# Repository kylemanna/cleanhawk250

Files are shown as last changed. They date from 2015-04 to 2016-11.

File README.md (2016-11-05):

# CleanHawk 250 Quadcopter Power Distribution Board for Emax 250

This document outlines the basic tasks to get the CleanHawk 250 Power Distribution Board (PDB) up and flying.

**Documentation can be found at the [CleanHawk250 GitHub repository](https://github.com/kylemanna/cleanhawk250).**

## Overview

The goal of the CleanHawk 250 PDB is to simplify wiring and imporve integration and reliability.  The printed circuit board replaces the bottom carbon fiber frame support on the Emax 250 / Nighthawk 250 quadcopters.

### Buy It Now

* [Tindie](http://bit.ly/1HMsioh)
* [Amazon](http://amzn.to/2fEIMti)

### Features

* **3-4S compatible**
* Designed for **KISS 18A ESCs**, ReadyToFly/Witespy's BearHug should fit just fine, and have pads for traditional ESCs. Hoping that the new Emax BLHeli Oneshot ESCs fit.
* **3A @ 5V** for flight computer, OSD, and LEDs (i.e. WS2812), telemetry/BT, etc. (85%+ efficient).
* **3A @ 9V** for FPV camera, vtx, and LEDs. (92%+ efficient),
* **(6) RGB LEDs**. 4 on bottom, 2 on top (not sure if top will be useful). Testing waters here. User configurable color by changing resistors. Plan is to do red on the rear and white up front.
* **FPV LC filter** that can select between 9V or 5V for feeding cameras and FPV transmittter,
* Multiple soldering points for accessories on the VBAT, 9V, and 5V rail. Helps to contain the wiring mess.
* **Battery voltage divider** for dividing the voltage down to something manageable for the Frsky D4R-II.
* Optional bulk capacitance near the ESCs to help smooth out ripples.
* Centralized battery input pads to keep the high current paths through the board as short as possible
* **2oz copper** for efficiency and electroless nickel immersion gold plating for solderability.
* Sufficient copper keep out area surrounding the mounting holes
* Shielded inductors to reduce switching power supply noise.

### What's Included

* (1) CleanHawk 250 Power Distribution Board with all surface mount components installed.
* (1) 1x4 pin header for the auxiliary port
* (1) 1x6 pin header for the ESC and flight controller port
* (3) 2x2 pin header for respective power supply outputs (5V, 9V, Filtered)

### Recommended Additional Components

#### Wire Extension Cables

It is recommended to use Dupont female to female cable connectors to wire the PDB to the receiver and flight controller. Available on [Amazon in 10cm length](http://amzn.com/B00KOL5BCC).

Dupont cables

An alternative to these are male to male servo extension headers such as [these from Amazon](http://amzn.com/B00FGLSTY2).

Servo extension

#### Angled Pin Headers

Consider picking up 90° 0.1" angled pin headers. Single row pin headers aid in mounting KISS ESCs.  Double row pin headers are very useful if the front/rear pin P1-P4 headers for LED connections.

#### XT60 Battery Connector and Pigtail

An XT60 connector is the most popular battery connector and a pigtail easily connects to the center battery pads.

XT60 Pigtail

[MassiveRC carries XT60 connectors](http://bit.ly/1OBGKkD) and are perfect compliment for your PDB order.

#### Electrical Tape

Electrical tape is a critical requirement to insulate parts mounted on the PCB (i.e. KISS ESCs) to prevent wearing through the solder mask.  I stick to [3M Super33](http://amzn.com/B00004WCCL).  I recommend sticking some to the part of the PDB immediately below any mounted components such as ESCs.

#### Cable Ties

Strap down wires or ESCs to secure them.  Things will vibrate or rattle and eventually fail unless secured.

## Quick Start Guide

### Step 1 — Install Battery Wires

Battery wires up to 12 AWG are installed to the large through hole pads in the center of the board.  Due to the massive copper area surrounding the pads to transfer large amounts of current to the ESCs, **a large amount of heat is necessary to solder to this pad**.  *Turn the soldering iron temperature up, feed solder to help transfer heat from the tip to the pad, and be patient.*

### Step 2 — Install Pin Headers

The `P9` header is critical for flight and should be installed first.  All other headers are *optiona*l and pilots should refer to the [pin headers documentation](PinHeaders.md) for more details.

Verify that the Dupont cables or servo extensions are available to connect `P9` to the flight controller.

### Step 3 — Configure LC Filter and FPV Gear

The LC filter should be bridged to the 9V side for most FPV gear.  Verify this is valid for your gear and modify `JP1` if needed.  More details in the [pin headers documentation](PinHeaders.md).

### Step 4 — Install ESCs

Mount the ESCs to the board with **some insulation such as heat shrink or 3M Super33 to avoid shorts** that could occur should they wear through the black solder mask.  More details in the [ESC documentation](ESCs.md).

### Step 5 — Install on Quadcopter

Install the board in place of the bottom carbon fiber plate.  Verify that all screws and hardware fit in the designated area and aren't rubbing on the PDB. Note that there are recesses on the board around all mounting holes where copper has been removed to prevent issues.  **Failure to remove any objects that are touching the PDB could damage the PDB and cause a short and in extreme cases a fire.** Don't be on the news or YouTube with a flaming CleanHawk quad copter!

## Known Issues

Review the [Change Log](http://bit.ly/1GxYUxc) for more details.

### v1.0
* 5V and GND silkscreen labels flipped on first build, but copper traces are correct. Refer to images or verify with multipmeter before powering flight controller.
* QR code placement is a little off and leads to now [defunct bit.ly bundle](http://bitly.is/1aG0YLU).  Thanks bit.ly!  It'd be nice if I could change the destination URL to the GitHub page instead.
* `JP1` / `FILTER_SEL`'s +5V pad isn't hooked upto `+5V` and won't work as expected.  Instead jump the center pad of `JP1` / `FILTER_SEL` to the `+5V` pin of `P2` or `P3`.

### v1.1

* None

## Additional Reading

* [RC Groups Forum Thread](http://bit.ly/1aFZpxj)
* [Hackaday Project Page and Build Log](http://bit.ly/1aG09m9)
* [Imgur Image Gallery](http://bit.ly/1aG00z3)
* [Change Log](http://bit.ly/1GxYUxc)

## License

This work is licensed under the Creative Commons Attribution-ShareAlike 4.0 International License. To view a copy of this license, visit http://creativecommons.org/licenses/by-sa/4.0/ or send a letter to Creative Commons, PO Box 1866, Mountain View, CA 94042, USA.

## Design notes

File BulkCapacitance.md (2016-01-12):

# Bulk Capacitance

The board has provisions for 4 additional tantalum capacitors to help improve throttle response or smooth out ripple depending on battery and ESC combinations.  The parts aren't included as they are cost prohibitive and not needed by most people.

## Capacitor Selection

The pads are an industry standard `EIA 7343 metric` size.  Capacitors installed here **must be ultra low ESR** to have their desired effect. I also highly recommend following industry standard techniques for voltage derating capacitors to avoid failure, that is to say, pick a voltage rating of about double the nominal voltage of your batteries.

Links to findchips.com for a list of distributors:
* [AVX `TCJY336M025R0060`](http://bit.ly/1RJzCWf)
* [KEMET `T521V336M025ATE060`](http://bit.ly/1mUuXWo)

Also consider eBay.com and AliExpress.com for the parts as well.

## Installation

The unpopulated bulk capacitors are labeled with identfiers: `C1`, `C2`, `C3`, `C4`.

The line or bar on the capcitor marks the anode and should be orientated in the direction that places that anode nearest the `+` symbol on the PCB silkscreen.

These components are easily soldered with a traditional soldering iron and leaded or lead-free solder with flux.

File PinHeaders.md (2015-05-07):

# CleanHawk 250 Pin Header Description

Most pin headers are labeled on the silkscreen.  When in doubt, verify with this document and a multimeter.

Only the P9 header is required to fly.

**Pin 1 is marked by a square pad.**

## P9 - Primary ESC Header

Provides +5V power and ground to the flight controller and serves as a connection for ESC control signals.

**Note**: The first batch *v1.0* of boards has the silkscreen incorrectly labeled, but the electrical wires are correct.  These boards are marked with white paint over the silkscreen to avoid confusion. 

Pin | Function
----|---------
1   | GND
2   | +5V
3   | ESC1
4   | ESC2
5   | ESC3
6   | ESC4

P9

## P6 - Auxiliary Receiver Header

Provides signals commonly used for telemetry on RC Receivers such as the FrSky D4R-II.

Pin | Function
----|---------
1   | +BATT
2   | GND
3   | AD2
4   | GND

The `AD2` pin can be directly connected to a FrSky receiver and usedin place of existing voltage dividers.  It works with up to 4S lipos. `AD2 = +BATT * 2.32 / (10 + 2.32)`.  The telmetry gain will need to be adjusted appropriately, **verify with a multimeter before flying**.

P6

## P7 - 5V Header

Provides access to 5V regulator output.  Use for auxiliary flight systems.

Pin | Function
----|---------
1   | +5V
2   | GND
3   | +5V
4   | GND

P7

## P8 - 9V Header

Provides access to 9V regulator output.  Use for auxiliary flight systems.

Pin | Function
----|---------
1   | +9V
2   | GND
3   | +9V
4   | GND

P8

## P5 - LC Filter Header

Provides access to LC filtered regulator output.  The source of the filter is selectable with the `JP1` Filter Sel solder pads.  Bridge the pads to select desired output voltage.  Most people power FPV gear will want 9V bridged to the center pad of `JP1` and power the video transmitter (VTX) and the FPV camera.

Pin | Function
----|---------
1   | +FLT
2   | GND
3   | +FLT
4   | GND

P5
JP1

## P1 and P2 - Front and Rear Auxiliary Power

Intended to power LEDs or other accessories.

Pin | Function
----|---------
1   | +9V
2   | GND
3   | +5V
4   | GND

P1
P2

## P3 and P4 - Front and Rear Auxiliary Power

Intended to power LEDs, cameras fed directly from batteries or other accessories.

Pin | Function
----|---------
1   | +BATT
2   | GND
3   | +5V
4   | GND

P3
P4

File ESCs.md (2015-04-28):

# Electronic Speed Controllers

The board is designed in such a way that it allows for ultra minature ESCs such as Flyduino's KISS 18A ESCs as well as traditional ESCs.

## Wiring

The ESC wires are routed to the flight controller via the `P9` pin header.  The traces on the board run to the corresponding pads where the ESCs are to be mounted.  Power is provided via 2oz copper and very short distance from the battery solder pads for optimum efficiency.

### Pinout

Pin | Function
----|---------
1   | `BATT+` / `LIPO+` - Directly connected to battery inputs
2   | `SIG` - connect to the PWM input of the ESC
3   | `GND` - connected to LIPO- on the PCB, *only needed for opto isolated ESCs* but doesn't hurt to connect
4   | `BATT-` / `LIPO-` - Directly connected to battery inputs

ESC1

### KISS 18A ESCs

These ESCs can be mounted directly to 90° pin headers and soldered to the ESC boards.  This results in an ultra clean look.  Ensure the ESCs are secured with an additional mechanism (not just pin headers) to prevent them from vibrating in flight.

### Other ESCs

The holes on the board will accomodate up to 20AWG wire to power any variety of ESCs that exist.  Ideally the ESC would be small enough to mount in the space created for the KISS ESCs.

## Mounting

**Always provide isolation between ESCs mounted directly to the PCB with some sort of insulator such as 3M Super33 electrical tape or heatshrink.**  Failure to do this could result in a short and likely a crash that would follow the instant after.

The recommend mounting procedure is to place Super33 electrical tape on the PDB to insulate the ESC from the PDB.  A cable tie can then be used to wrap around the PDB to strap the ESC down to some of the existing holes or around the board itself.

**Ensure ESCs are secure before flight!**

## Future

It would be nice if the RC community could agree on a standard pinout and spacing of the ESC inputs so that pin headers could be utilized in the future.

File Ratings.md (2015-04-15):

# Ratings

## Battery:

The board is rated for 3-4S and could possibly be modded to reach 5S (for the crazy people).

Up to 80A of current is possible thanks to ultra traces and wide copper pours.

## Regulators

Both the 5V and 9V regulator are capable of up to 3A.

The regulators and associated circuitry surrounding them will get **hot over 2A of current, caution is advised at higher current levels.**  That said, these regulators vastly outpreform all linear regualtors for those looking to fly with higher current accessories such as high brightness LEDs and high power video transmitters.

## LC Filter

LC filter voltage must remain below 12V and under 800 mA.

## Protections

* The on-board regulators are protected from reverse voltage hook-up (oops).
* The on-board regulators have a thermal overload that will shut them down if they are momentarily abused.

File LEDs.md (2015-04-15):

# RGB LEDs

The CleanHawk 250 PDB comes with 6 standard brightness RGB LEDs to help the pilot determine orientation in flight.  By default the front LEDs are near white (some variance is observed due to 1% resistor manufacturing tolerance) and the rear LEDs are red.

## Additional LEDs

The LEDs are not high brightness and pilots are encouraged to use the P1-P4 headers to install brigher LEDs if desired and mount them a more visible location.

## Changing the LED Color

The 3 LEDs on each end of the board are wired in series and color can be changed by modifying the appropriate resistors.  To change the color, modify the resistor values to create any color in the rainbow.

The resisor size is `0603` and different resistor values can be purchased from places like Digi-Key.  Choosing a resistor value is matter of obtaining the target current as it relates to the other colors to obtain the desired overall color.

The LEDs are powered by the 9V regulator and each color is wired in with three LEDs in series.

### Front LEDs

Id | LED Color | Default Resistor Value
---|-----------|------------
R1 | Blue      | 68 ohms
R2 | Red       | 120 ohms
R3 | Green     | 68 ohms

### Rear LEDs

Id | LED Color | Default Resistor Value
---|-----------|------------
R4 | Blue      | not installed
R5 | Red       | 120 ohms
R6 | Green     | not installed

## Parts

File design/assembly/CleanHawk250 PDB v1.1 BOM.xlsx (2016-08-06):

Item # | Description | Designator | Qty | Pop | Manufacturer # | Distrib | Distrib # | Package | Value
1 | LED SMD RGB 5x5mm | D1,D2,D3,D4,D5,D6 | 6 | 6 | XCH-5050RGB | Alibaba | XCH-5050RGB (http://www.aliexpress.com/snapshot/6522467977.html?orderId=66088301478625) | 5050_RGB_LED | LED_5050_RGB
2 | CAP CER 0.1UF 16V 5% X7R 0603 | C8,C17 | 2 | 2 | CL10B104JO8NNNC | Arrow | CL10B104JO8NNNC | C_0603 | 100nF
3 | CAP CER 18PF 50V 5% NP0 0603 | C11,C20 | 2 | 2 | CL10C180JB8NNNC | Verical | CL10C180JB8NNNC | C_0603 | 18pF
4 | CAP CER 680PF 50V 5% X7R 0603 | C15,C23 | 2 | 2 | CL10B681JB8NNNC | Arrow | CL10B681JB8NNNC | C_0603 | 680pF
5 | CAP CER 8200PF 50V 10% X7R 0603 | C16,C24 | 2 | 2 | CL10B822KB8NNNC | Arrow | CL10B822KB8NNNC | C_0603 | 8.2nF
6 | CAP CER 22UF 16V 20% X5R 1206 | C12,C13,C14,C21,C22 | 5 | 5 | CL31A226MOCLNNC | Verical | CL31A226MOCLNNC | C_1206 | 22uF/16V
7 | CAP CER 10UF 35V 10% X5R 1206 | C7,C9,C10,C18,C19 | 5 | 5 | GMK316BJ106KL-T | Avnet | GMK316BJ106KL-T | C_1206 | 10uF/35V
8 | FIXED IND 820UH 730MA 1.5 OHM | L1 | 1 | 1 | SRR1260-821K | DigiKey | SRR1260-821KTR-ND | Choke_SMD_12x12mm_h6mm | 820uH
9 | FIXED IND 8.2UH 5.7A 19.5 MOHM | L2,L3 | 2 | 2 | SRR1260-8R2Y | Verical | SRR1260-8R2YTR-ND | Choke_SMD_12x12mm_h6mm | 8.2uH
10 | DIODE SCHOTTKY 40V 3A SMB | D7,D8,D9,D10 | 4 | 4 | B340LB-13-F | Verical | B340LB-13-F | Diode-SMB_Standard | B340LB
11 | RES SMD 2.32K OHM 1% 1/10W 0603 | R8 | 1 | 1 | MCR03ERTF2321 | DigiKey | RHM2.32KCFTR-ND | R_0603 | 2.32k/1%
12 | RES SMD 10K OHM 1% 1/10W 0603 | R7,R10,R15 | 3 | 3 | MCR03ERTF1002 | DigiKey | RHM10.0KCFTR-ND | R_0603 | 10k/1%
13 | RES SMD 78.7K OHM 1% 1/10W 0603 | R9,R14 | 2 | 2 | MCR03ERTF7872 | DigiKey | RHM78.7KCFTR-ND | R_0603 | 78.7k
14 | RES SMD 976 OHM 1% 1/10W 0603 | R16 | 1 | 1 | MCR03ERTF9760 | DigiKey | RHM976CFTR-ND | R_0603 | 866/1%
15 | RES SMD 1.91K OHM 1% 1/10W 0603 | R11 | 1 | 1 | MCR03ERTF1911 | DigiKey | RHM1.91KCFTR-ND | R_0603 | 1.91k/1%
16 | RES SMD 68 OHM 5% 1/10W 0603 | R1,R3, DNP: R4,R6 | 4 | 2 | MCR03ERTJ680 | DigiKey | RHM68CGTR-ND | R_0603 | 68
17 | RES SMD 120 OHM 5% 1/10W 0603 | R2,R5 | 2 | 2 | MCR03ERTJ121 | DigiKey | RHM120CGTR-ND | R_0603 | 120
18 | IC REG BUCK ADJ 3A 8SOIC | U1,U2 | 2 | 2 | TPS54331DR | Alibaba | TPS54331DR (http://www.aliexpress.com/snapshot/6525845753.html?orderId=66107612918625) | SOIC-8-N-1EP | TPS54331
19 | CAP TANT 100UF 16V 10% 2917 | C5,C6 | 2 | 2 | TAJD107K016RNJ | Alibaba | TAJD107K016RNJ | TantalC_SizeD_EIA-7343_Reflow | 100uF/16V
19 |  |  |  | 47
 | No Pop
20 | Printed Circuit Board | - | 1 | 1 | PCB Way | PCB Way
21 | CONN HEADER .100" SNGL STR 40POS | P6,P9 | 2 | 2 |  | Alibaba |  | Pin_Header_Straight_1x0X | CONN_01X0X
22 | CONN HEADER VERT DUAL 40POS | P1,P2,P3,P4,P5,P7,P8 | 7 | 7 |  | Alibaba |  | Pin_Header_Straight_2x02 | CONN_02X02
23 | RES SMD 169k OHM 5% 1/10W 0603 | R12 | 1 | 0 |  |  |  | R_0603 | 169k
24 | RES SMD 28k OHM 5% 1/10W 0603 | R13 | 1 | 0 |  |  |  | R_0603 | 28k
25 | CAP POLYMER SMD 33uF 7343 | C1,C2,C3,C4 | 4 | 0 | TCJY336M025R0060 |  |  | TantalC_SizeD_EIA-7343_Reflow | 33uF/25V
26 | RES SMD 68 OHM 5% 1/10W 0603 | R4,R6 | 2 | 0

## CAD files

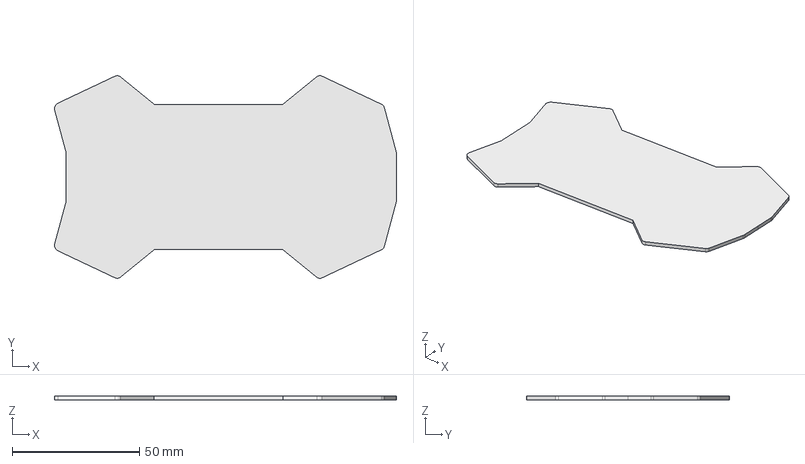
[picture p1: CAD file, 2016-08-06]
design/FreeCAD/Board Outline.fcstd
134.5 x 79.7 x 1.60 mm

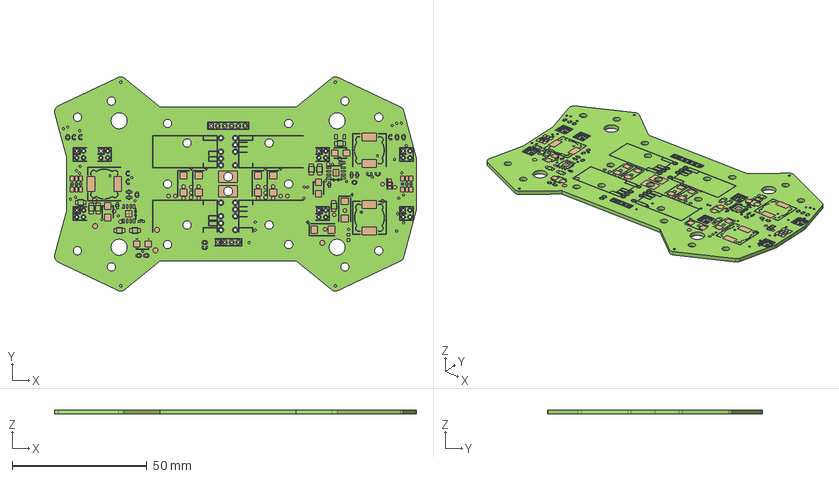
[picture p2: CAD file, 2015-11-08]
mechanical/cleanhawk250-pdb.fcstd
134.5 x 79.7 x 1.67 mm
Board
bPad_107
tPad_108
B_SilkS_36
F_SilkS_37

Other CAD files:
design/FreeCAD/Board Outline.dxf
mechanical/cleanhawk250-pdb.dxf
mechanical/cleanhawk250-pdb.stl

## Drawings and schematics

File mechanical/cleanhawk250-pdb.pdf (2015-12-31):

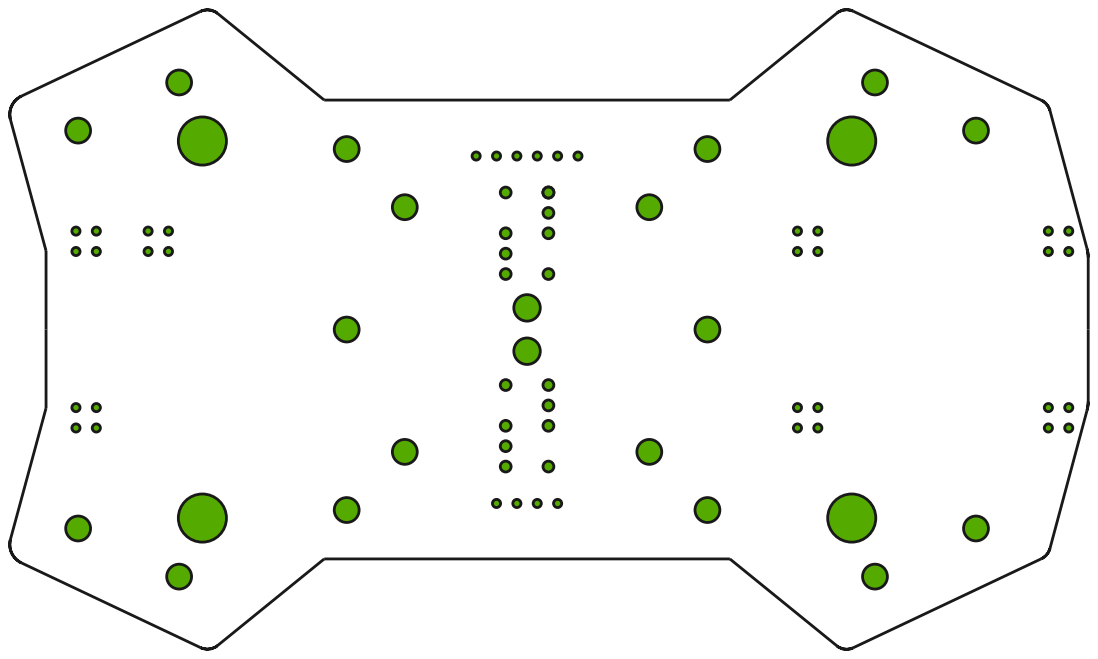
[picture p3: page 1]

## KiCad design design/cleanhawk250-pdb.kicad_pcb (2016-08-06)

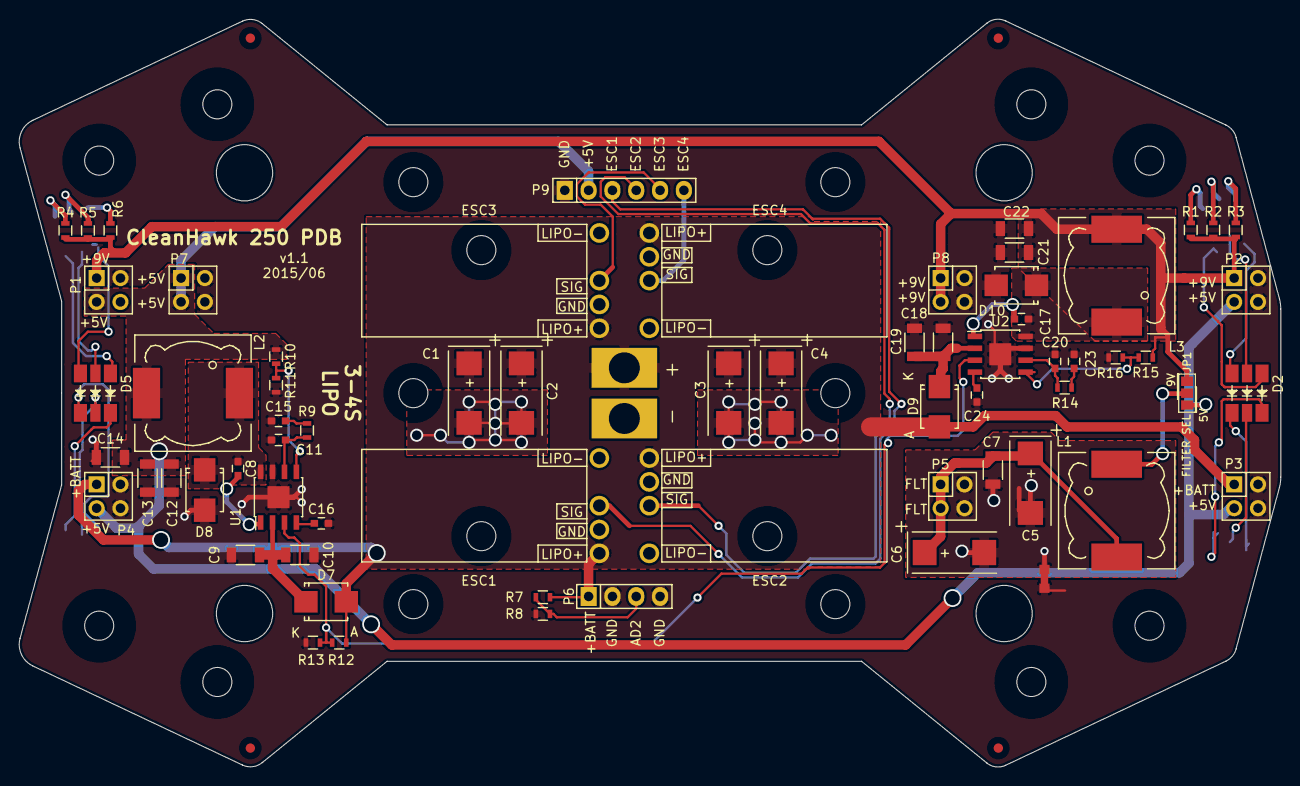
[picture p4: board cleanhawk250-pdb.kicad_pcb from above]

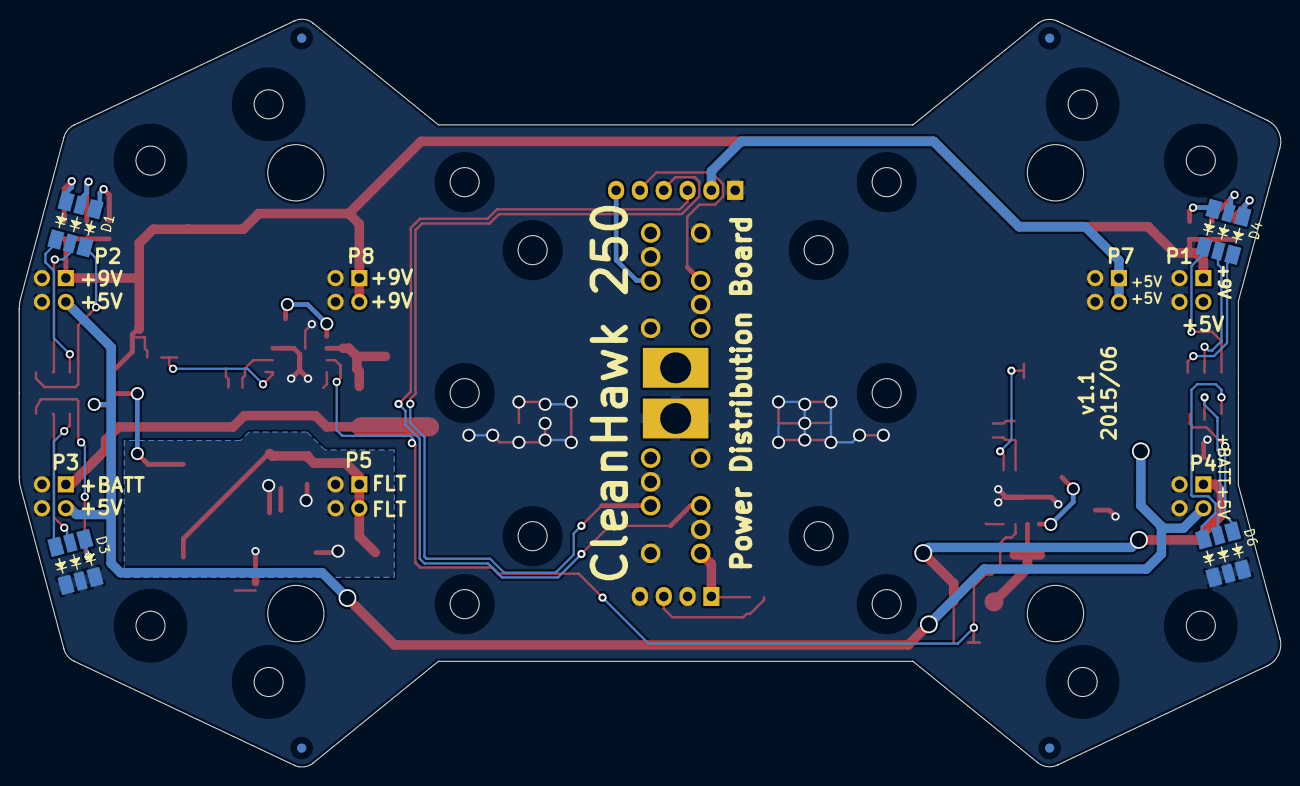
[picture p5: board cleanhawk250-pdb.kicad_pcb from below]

Board: 2 copper layers, 134.5 x 79.7 mm, 80 parts (8 on the bottom side), 45 nets.

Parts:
C1, C2, C3, C4: 33uF/25V/np; TantalC_SizeD_EIA-7343_Reflow
C5, C6: 100uF/16V; TantalC_SizeD_EIA-7343_Reflow
C7, C9, C10, C18, C19: 10uF/35V; C_1206
C8, C17: 100nF; C_0603
C11, C20: 18pF; C_0603
C12, C13, C14: 22uF/10V; C_1206
C15, C23: 680pF; C_0603
C16, C24: 8.2nF; C_0603
C21, C22: 22uF/16V; C_1206
D1, D2, D3, D4, D5, D6: RGB_LED_5050; LED_5050_RGB
D7, D8, D9, D10: B340LB; Diode-SMB_Standard
ESC1, ESC2, ESC3, ESC4: KISS_ESC_18A; Kiss_ESC_18A_v1.1
F1, F2, F3, F4, F5, F6, F7, F8: SPECIAL; FIDUCIAL_1MM
FRAME1: SPECIAL; Emax250_Bottom_Holes
JP1: FILTER SEL; AB2_SJMP_03-1
JP2: JUMPER; NetTie-I_Connected_SMD
L1: 820uH; Choke_SMD_12x12mm_h6mm
L2, L3: 8.2uH; Choke_SMD_12x12mm_h6mm
P1, P2, P3, P4, P5, P7, P8: CONN_02X02; Pin_Header_Straight_2x02
P6: CONN_01X04; Pin_Header_Straight_1x04
P9: CONN_01X06; Pin_Header_Straight_1x06
R1, R3: 68; R_0603
R2, R5: 120; R_0603
R4, R6: 68/np; R_0603
R7, R10, R15: 10k/1%; R_0603
R8: 2.32k/1%; R_0603
R9, R14: 78.7k; R_0603
R11: 1.91k/1%; R_0603
R12: 169k/np; R_0603
R13: 28k/np; R_0603
R16: 976/1%; R_0603
U1, U2: TPS54331; SOIC-8-1EP_3.9x4.9mm_Pitch1.27mm
W1: WIREPADS; WirePads_12AWG_TH

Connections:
+5V: C12.1, C13.1, C14.1, JP1.3, L2.2, P1.3, P2.3, P3.3, P4.3, P7.1, P7.3, P9.2, R10.1
+9V: C21.1, C22.1, JP1.1, L3.2, P1.1, P2.1, P8.1, P8.3, R1.2, R2.2, R3.2, R4.2, R5.2, R6.2, R15.1
+BATT: C1.1, C2.1, C3.1, C4.1, D7.2, D9.2, ESC1.1, ESC2.1, ESC3.1, ESC4.1, P3.1, P4.1, P6.1, R7.2, R12.1, W1.+
ESC1: ESC1.2, P9.3
ESC2: ESC2.2, P9.4
ESC3: ESC3.2, P9.5
ESC4: ESC4.2, P9.6
GND: C1.2, C2.2, C3.2, C4.2, C9.2, C10.2, C11.2, C12.2, C13.2, C14.2, C15.2, C16.2, C18.2, C19.2, C20.2, C21.2, C22.2, C23.2, C24.2, D3.4, D3.5, D3.6, D6.4, D6.5, D6.6, D8.2, D10.2, ESC1.3, ESC1.4, ESC2.3, ESC2.4, ESC3.3, ESC3.4, ESC4.3, ESC4.4, JP2.1, P1.2, P1.4, P2.2, P2.4, P3.2, P3.4, P4.2, P4.4, P6.2, P6.4, P7.2, P7.4, P8.2, P8.4, P9.1, R8.2, R11.2, R13.2, R16.2, U1.7, U1.9, U2.7, U2.9, W1.-
GNDA: C5.2, C6.2, C7.2, JP2.2, P5.2, P5.4
unnamed: C5.1, C6.1, C7.1, L1.2, P5.1, P5.3
unnamed: C8.1, U1.1
unnamed: C8.2, D8.1, L2.1, U1.8
unnamed: C9.1, C10.1, D7.1, U1.2
unnamed: C11.1, R9.1, U1.6
unnamed: C15.1, R9.2
unnamed: C16.1, U1.4
unnamed: C17.1, U2.1
unnamed: C17.2, D10.1, L3.1, U2.8
unnamed: C18.1, C19.1, D9.1, U2.2
unnamed: C20.1, R14.1, U2.6
unnamed: C23.1, R14.2
unnamed: C24.1, U2.4
unnamed: D1.1, R1.1
unnamed: D1.2, R2.1
unnamed: D1.3, R3.1
unnamed: D1.4, D2.3
unnamed: D1.5, D2.2
unnamed: D1.6, D2.1
unnamed: D2.4, D3.3
unnamed: D2.5, D3.2
unnamed: D2.6, D3.1
unnamed: D4.1, R4.1
unnamed: D4.2, R5.1
unnamed: D4.3, R6.1
unnamed: D4.4, D5.3
unnamed: D4.5, D5.2
unnamed: D4.6, D5.1
unnamed: D5.4, D6.3
unnamed: D5.5, D6.2
unnamed: D5.6, D6.1
unnamed: JP1.2, L1.1
unnamed: P6.3, R7.1, R8.1
unnamed: R10.2, R11.1, U1.5
unnamed: R15.2, R16.1, U2.5
REG_EN: R12.2, R13.1, U1.3, U2.3

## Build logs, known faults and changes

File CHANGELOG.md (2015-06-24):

# Change Log
All notable changes to this project will be documented in this file.
This project adheres to [Semantic Versioning](http://semver.org/).

## [1.1] - 2015-06-23

### Added
- Silkscreen labels on bottom.

### Removed
- QR Code on the bottom.

### Changed
- Fixed missing trace between 5V net and JP1 solder jumper for 5V filter selection.
- Correct silkscreen label for P9 (ESC connector).
- Tweak pad layout for LEDs.
- Tweak pad layout for regulator chip.

## [1.0] - 2014-03-31
### Added
- Initial design.

[1.1]: https://github.com/kylemanna/cleanhawk250/compare/v1.0.0...HEAD
[1.0]: https://github.com/kylemanna/cleanhawk250/compare/v0.1.0...v1.0.0

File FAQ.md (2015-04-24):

# Frequently Asked Questions

## What are R12 and R13?  Why aren't they populated?

These two resistors would set the input cut out voltage to shut the 5V and 9V regulators off.  This would protect the lipo batteries from over discharging.  The reality is that even if the primarily regulators shut off, the ESCs would continue draining the batteries (i.e. left overnight).

To avoid surprises such as loss of control, these resistors are not populated and the regulators operate as low as they can go.  With 3S and above, the regulators will continue to operate long after the craft falls out of the sky.

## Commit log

2015-04-13 README: Add bolt to features list
    * Highlight main selling points.
2015-04-15 LED: Initial commit
    * LEDs and stuff
    * Bedazzle the quad
2015-04-15 ESC: Initial Commit
    * KISS ESCs are the stars
    * Then everyone else!
2015-04-15 README: Add battery wries
    * Power in to get power out.
2015-04-15 README: Dedicated step for battery wires
    * Keep it simple
2015-04-15 README: Add XT60 connector recommendation
    * Don't forget!
2015-04-15 ESC: Add pinout
    * Add picture of ESC layout
    * Add pinout
2015-04-23 Headers: Correct filter header
    * Oops.
2015-04-28 ESCs: Clarify signal ground wire.
    * Help reduce confusion.
2015-05-07 Headers: Mention camera
    * Mention that the +BATT can be used to power a camera.
2015-05-19 README: Add JP1 +5V Issue
    * Oops on my part. Not the end of the world though.
2015-06-24 changelog: Initial commit
    * Keep track of what changes. Simple.
2015-06-24 changelog: Clarify v1.1 JP1 5V fix
    * More descriptive.
2015-11-08 mechanical: Add mechanical drawings of the PCB
    * Useful for people wanting to build things on top of it.
    [cleanhawk250-pdb.fcstd]
2015-11-08 mechanical: Add STL format for GitHub
    * This might be useful if GitHub's 3D viewer is any good.
    [cleanhawk250-pdb.stl]
2015-12-31 mechanical: Add more drawings
    * Add the PDF which was verified to be correct as long as not scaled
    when printed.
    * Unable to verify dxf, but included anyways.
    [cleanhawk250-pdb.dxf]
2016-08-06 design: Add v1.1.0 release of design files
    * Copied from my private repository.
    * Private commit hash: 96499ad338b4d3217b69c7f2c7c0db7a9b2d369a
    [Board Outline.dxf, Board Outline.fcstd, CleanHawk250 PDB v1.1 BOM.xlsx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]
